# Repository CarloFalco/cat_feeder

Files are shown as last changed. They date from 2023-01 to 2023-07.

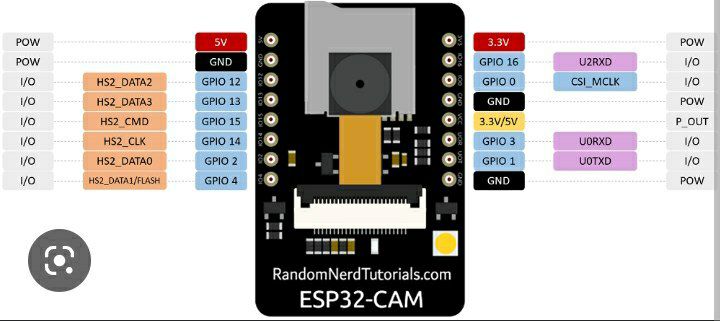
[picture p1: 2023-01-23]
EspCam_pinout.jpg

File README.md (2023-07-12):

# cat food dispenser 
| Cartella 		| Contenuto 		|
| --- 		| --- 			|
| 3D Model  	| File da stampare 	|
| Code  		| Codice 			|

## Requirements list:
- Webcam that allows you to take a photo on demand, and send it on telegram
- Proximity sensor that if it detects something in range takes a photo and sends it on telegram
- Food if requested by telegram dispenses food, every time it is asked it dispenses at least 20 kibbles
- Cap, it won't come off if dropped
- Power supply via usb cable
- System to vicariate it to the ground

## Component list:
1. [AM312](https://it.aliexpress.com/item/32921030810.html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)
1. [DS3230-180](https://it.aliexpress.com/item/1943129663.html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)
1. [ESP32-CAM-MB](https://it.aliexpress.com/item/1005003334474586.html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)
1. [OV2640-160/650nm](https://it.aliexpress.com/item/1005004518669324.html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)

## Printing component:

|  		|  		| 	|	|	||
| ---|--- | ---| ---|--- |--- |
| 1 | Hopper			| 76g 	| |7h 	|
| 2 | PortionWheel 		| 41g	| |4h 	|
| 3 | WheelCompartment 	| 59g	| |5h 	|
| 4 | electronic 		| 151g	| |16h 	|
| 5 | Bowl 				| 146g	| |15h 	|
| 6 | Shel 				| 214g	| |20h 	|
| 7 | Lid 				| 61g	| |5h 	|
| | 				| 		| |		|
|  		|  		|  748g	| |72h	|

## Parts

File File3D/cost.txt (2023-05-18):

1 	hopper 				76g 	7h
2	PortionWheel		41g		4h
3	wheelCompartment	59g		5h
4	electronic			151g	16h
5	Blow 				146g	15h
6	shel				214g	20h
7 	lid					61g		5h

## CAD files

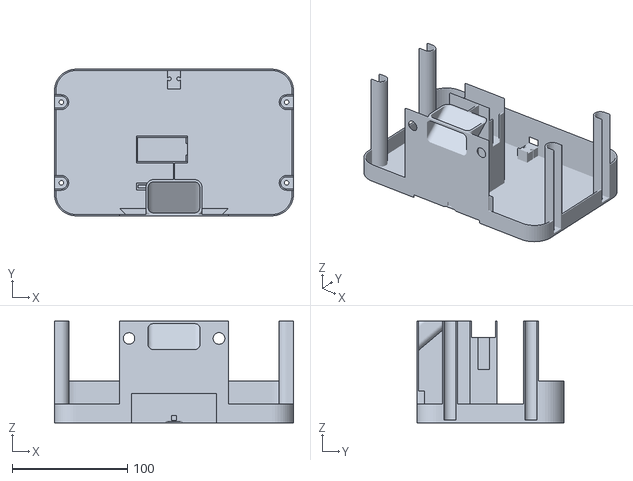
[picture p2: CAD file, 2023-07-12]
File3D/4-ElectronicsCompartment_V3.stl
207.2 x 127.2 x 88.2

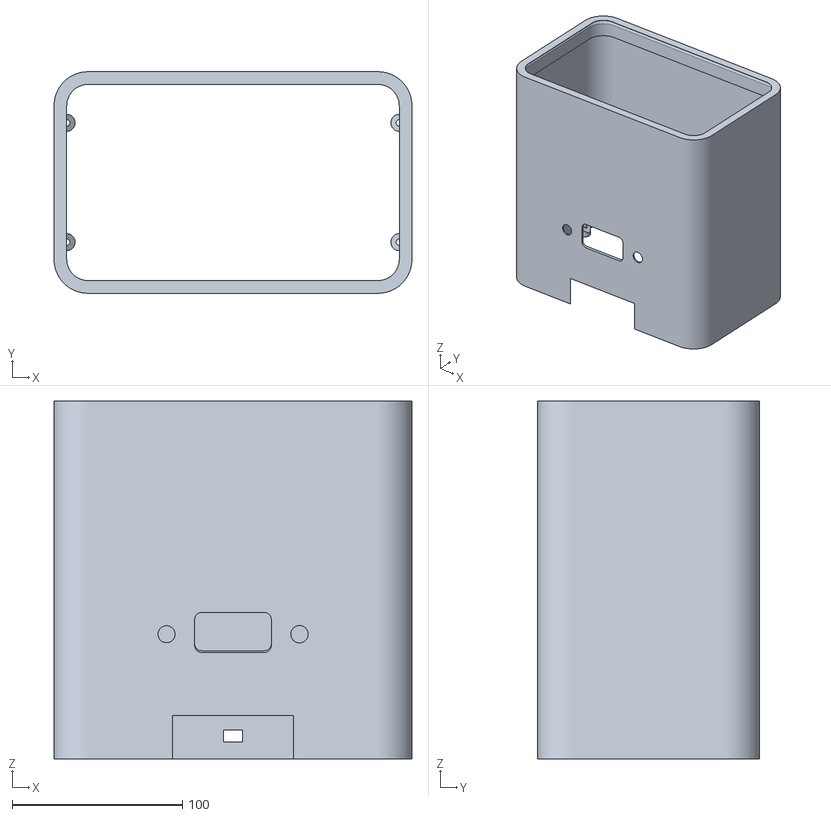
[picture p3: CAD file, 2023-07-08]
File3D/6-Shell_V2.stl
210.0 x 130.0 x 210.0

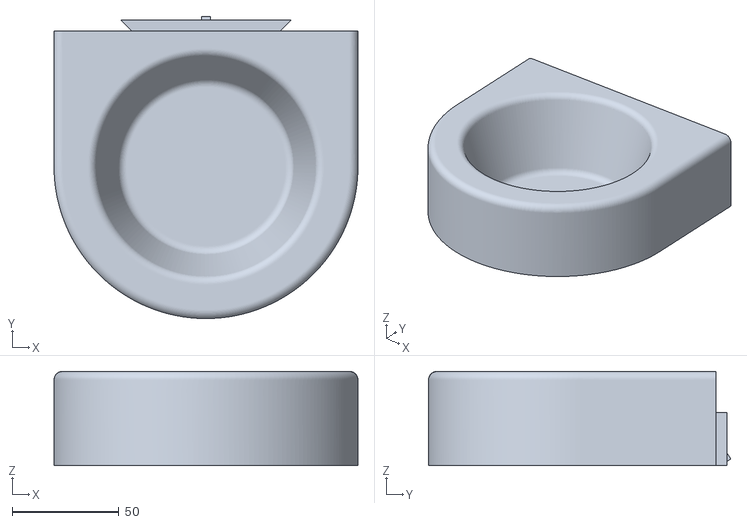
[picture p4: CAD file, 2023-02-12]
File3D/5-Bowl-103mm-diameter.stl
142.5 x 141.6 x 44.2

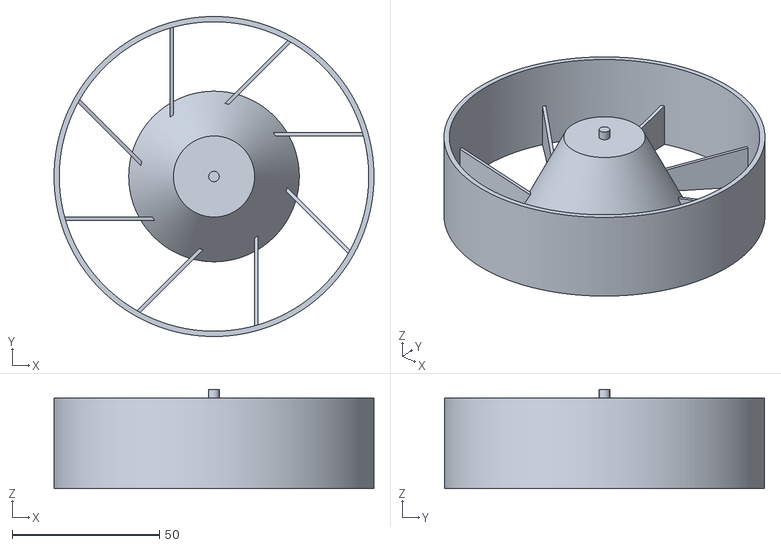
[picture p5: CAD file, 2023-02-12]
File3D/2-PortionWheel.stl
108.8 x 108.8 x 33.8

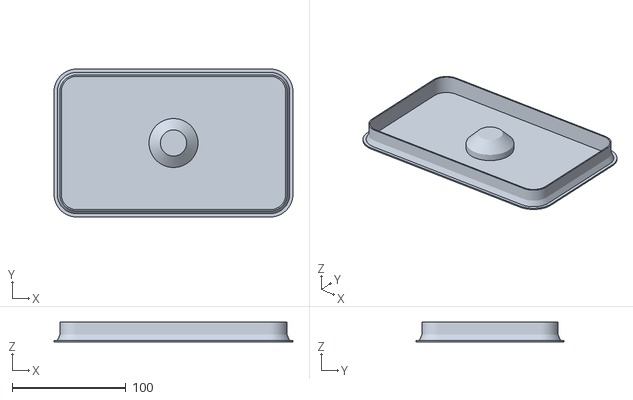
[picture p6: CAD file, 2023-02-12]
File3D/7-Lid.stl
210.0 x 130.0 x 17.2

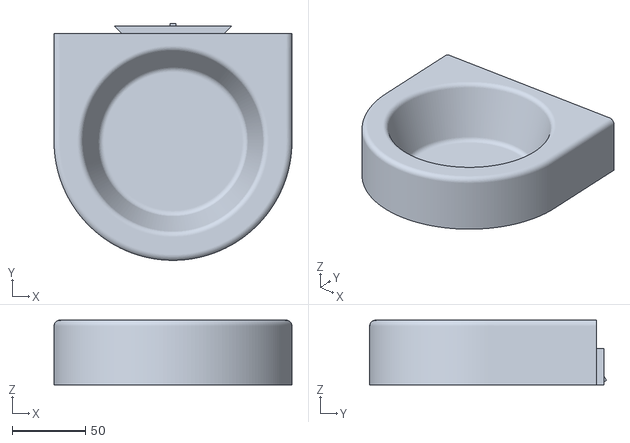
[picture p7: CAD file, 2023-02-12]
File3D/5-Bowl-123mm-diameter.stl
162.5 x 161.6 x 44.2

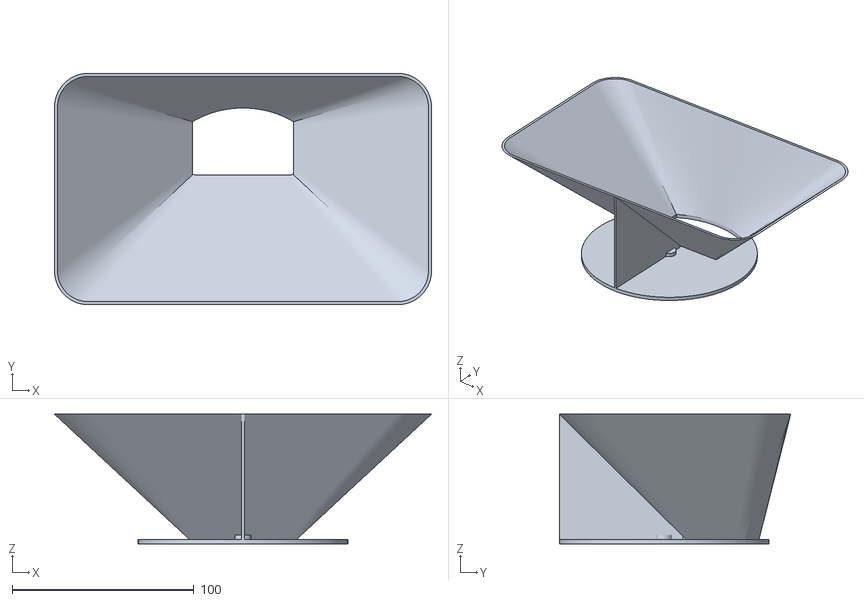
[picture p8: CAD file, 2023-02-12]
File3D/1-Hopper.stl
207.2 x 127.2 x 71.2

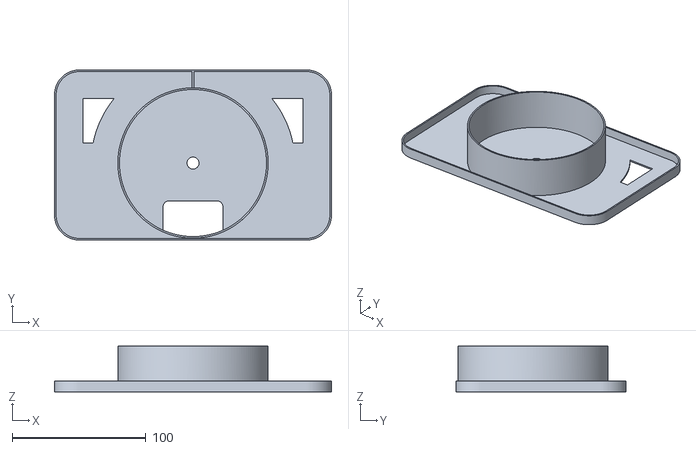
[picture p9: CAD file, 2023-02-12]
File3D/3-WheelCompartment.stl
207.2 x 127.2 x 34.4

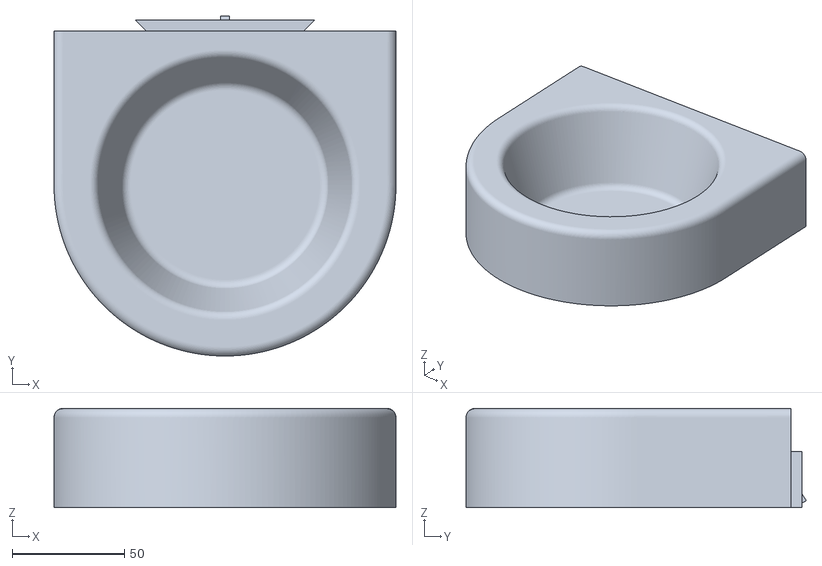
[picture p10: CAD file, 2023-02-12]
File3D/5-Bowl-113mm-diameter-default.stl
152.5 x 151.6 x 44.2

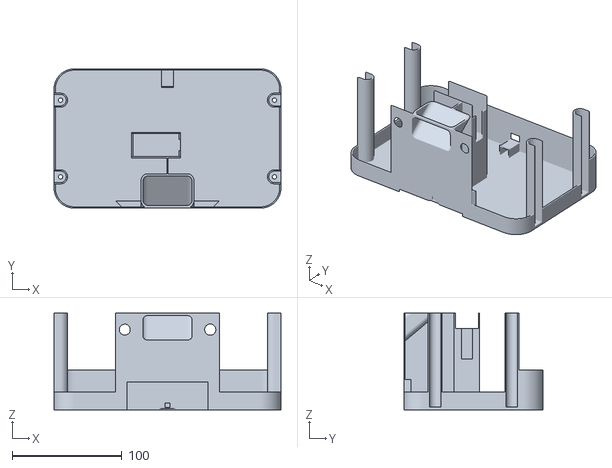
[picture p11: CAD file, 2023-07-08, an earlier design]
File3D/4-ElectronicsCompartment_V2.stl
207.2 x 127.2 x 88.2

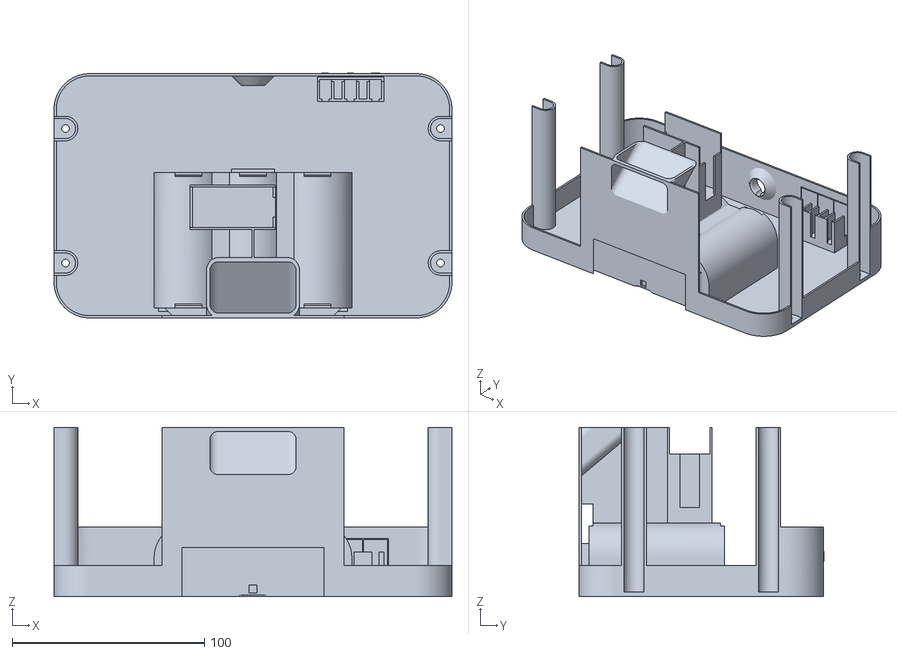
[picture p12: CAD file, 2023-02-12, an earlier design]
File3D/4-ElectronicsCompartment.stl
207.2 x 127.5 x 88.2

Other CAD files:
File3D/6-Shell.stl
File3D/FatPetFeeder-v4.40.f3d
File3D/FeederShell.f3d
File3D/PortaCrocchette.f3d

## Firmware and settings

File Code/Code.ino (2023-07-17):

#include <Arduino.h>
#include <WiFi.h>
#include <WiFiClientSecure.h>
#include "soc/soc.h"
#include "soc/rtc_cntl_reg.h"
#include "esp_camera.h"
#include <UniversalTelegramBot.h>
#include <ArduinoJson.h>

#include <freertos/FreeRTOS.h>
#include <freertos/task.h>
#include <ESP32Servo.h>

#include <EEPROM.h>
// Use @myidbot to find out the chat ID of an individual or a group
// Also note that you need to click "start" on a bot before it can
// message you

#include "Credential.h"

// FLASH
#define FLASH_LED_PIN 4
// SERVOMOTORE
#define MOS_SERVO_PIN 2
#define FEED_MAX_COUNT 6
#define SERVO_PIN 13
#define SERVO_MOVE_ON 95
#define SERVO_MOVE_OFF 90
#define FEED_INIT_COUNT 2
// SENSORE IR
#define IR_PIN 14
#define IR_DELAY 60  // tempo di delay tra un rilevamento ed un altro


// DEFINE FOR DEBUG
#define DEBUG_WIFI
#define DEBUG_FEEDER
#define DEBUG_NOTIFICATION


TaskHandle_t task1Handle;
TaskHandle_t task2Handle;
TaskHandle_t task3Handle;

typedef struct {
  String CurrentPhotoReqId;  // ID del utente che ha richiesto la foto
  String AuthId[4];          // ID degli utenti
  bool NotificationId[4];    // Flag di abilitazione notifiche utenti [1/0] abilitato/non abilitato

  bool stateIRpin;      // stato del sensore infrarossi
  bool stateSendPhoto;  // stato richiesta di foto
  bool stateFeedCat;    // stato richiesta feedcat
  bool stateFlash;      // stato flash
  int feedCount;        // quantità di cibo
  int eprom_good;       // eeprom non corrotta

} MyStruct;

MyStruct myStruct;

WiFiClientSecure clientTCP;

String BOTtoken = String(BOTtokenKey);
UniversalTelegramBot bot(BOTtoken, clientTCP);

Servo myservo;  // create servo object to control a servo

//Checks for new messages every 1 second.
int botRequestDelay = 500;
unsigned long lastTimeBotRan;

//Checks for new messages every 60 second.
int NotRequestDelay = IR_DELAY * 1000;
unsigned long lastTimeNot;

bool savetoEEPROM = false;

//CAMERA_MODEL_AI_THINKER
#define PWDN_GPIO_NUM 32
#define RESET_GPIO_NUM -1
#define XCLK_GPIO_NUM 0
#define SIOD_GPIO_NUM 26
#define SIOC_GPIO_NUM 27

#define Y9_GPIO_NUM 35
#define Y8_GPIO_NUM 34
#define Y7_GPIO_NUM 39
#define Y6_GPIO_NUM 36
#define Y5_GPIO_NUM 21
#define Y4_GPIO_NUM 19
#define Y3_GPIO_NUM 18
#define Y2_GPIO_NUM 5
#define VSYNC_GPIO_NUM 25
#define HREF_GPIO_NUM 23
#define PCLK_GPIO_NUM 22

void initWiFi_PwrOn(const char* ssid, const char* password) {
  WiFi.mode(WIFI_STA);
  WiFi.begin(ssid, password);
  clientTCP.setCACert(TELEGRAM_CERTIFICATE_ROOT);  // Add root certificate for api.telegram.org

  // Attesa della connessione
  while (WiFi.status() != WL_CONNECTED) {
    delay(1000);
#ifdef DEBUG_WIFI
    Serial.println("Connessione in corso...");
#endif
  }

#ifdef DEBUG_WIFI
  Serial.println("WiFi connected to " + String(ssid));
  Serial.println(WiFi.localIP());
#endif
}

// FUNZIONI RELATIVE ALLA EEPROM
void do_eprom_read() {

  EEPROM.begin(200);
  EEPROM.get(0, myStruct);

  if (myStruct.eprom_good == 11) {
    Serial.println("Good settings in the EPROM ");

    Serial.print("Notification: ");
    for (int i = 0; i < 4; i++) {
      Serial.print("\t");
      Serial.print(myStruct.NotificationId[i]);
    }
    Serial.println(".");

    Serial.println(myStruct.CurrentPhotoReqId);
    Serial.print("State IR: ");
    Serial.println(myStruct.stateIRpin);
    Serial.print("State sendphoto: ");
    Serial.println(myStruct.stateSendPhoto);
    Serial.print("State feedcat: ");    
    Serial.println(myStruct.stateFeedCat);
    Serial.print("State Flash: ");   
    Serial.println(myStruct.stateFlash);
    Serial.print("Count Num: ");
    Serial.println(myStruct.feedCount);

  } else {
    Serial.println("EPROM canot be read ");
    myStruct = {
      String(""),
      { String(CHAT_ID_1), String(CHAT_ID_2), String(""), String("") },
      { 1, 0, 0, 0 },
      false,                //stateIRpin
      false,                //stateSendPhoto
      false,                //stateFeedCat
      LOW,                  // stato flash
      FEED_INIT_COUNT,      // tempo di feed
      11                    // stato EEPROM
    };
    do_eprom_write();
  }
}

void do_eprom_write() {
  Serial.println("Writing to EPROM ...");
  EEPROM.begin(200);
  EEPROM.put(0, myStruct);
  EEPROM.commit();
  EEPROM.end();
}

// FUNZIONI RELATIVE ALLA FOTOCAMERA
void configInitCamera() {
  camera_config_t config;
  config.ledc_channel = LEDC_CHANNEL_0;
  config.ledc_timer = LEDC_TIMER_0;
  config.pin_d0 = Y2_GPIO_NUM;
  config.pin_d1 = Y3_GPIO_NUM;
  config.pin_d2 = Y4_GPIO_NUM;
  config.pin_d3 = Y5_GPIO_NUM;
  config.pin_d4 = Y6_GPIO_NUM;
  config.pin_d5 = Y7_GPIO_NUM;
  config.pin_d6 = Y8_GPIO_NUM;
  config.pin_d7 = Y9_GPIO_NUM;
  config.pin_xclk = XCLK_GPIO_NUM;
  config.pin_pclk = PCLK_GPIO_NUM;
  config.pin_vsync = VSYNC_GPIO_NUM;
  config.pin_href = HREF_GPIO_NUM;
  config.pin_sccb_sda = SIOD_GPIO_NUM;
  config.pin_sccb_scl = SIOC_GPIO_NUM;
  config.pin_pwdn = PWDN_GPIO_NUM;
  config.pin_reset = RESET_GPIO_NUM;
  config.xclk_freq_hz = 24000000;
  config.pixel_format = PIXFORMAT_JPEG;  //YUV422,GRAYSCALE,RGB565,JPEG
  config.grab_mode = CAMERA_GRAB_LATEST;
  config.frame_size = FRAMESIZE_HD;  // FRAMESIZE_ + QVGA|CIF|VGA|SVGA|XGA|SXGA|UXGA
  config.jpeg_quality = 10;          //10-63 lower number means higher quality
  config.fb_count = 4;

  // camera init
  esp_err_t err = esp_camera_init(&config);
  if (err != ESP_OK) {
    Serial.printf("Camera init failed with error 0x%x", err);
    delay(1000);
    ESP.restart();
  }

  // Drop down frame size for higher initial frame rate
  sensor_t* s = esp_camera_sensor_get();
  s->set_framesize(s, FRAMESIZE_HD);        // UXGA|SXGA|XGA|SVGA|VGA|CIF|QVGA|HQVGA|QQVGA
  s->set_brightness(s, 0);                  // -2 to 2
  s->set_contrast(s, 0);                    // -2 to 2
  s->set_saturation(s, 0);                  // -2 to 2
  s->set_special_effect(s, 0);              // 0 to 6 (0 - No Effect, 1 - Negative, 2 - Grayscale, 3 - Red Tint, 4 - Green Tint, 5 - Blue Tint, 6 - Sepia)
  s->set_whitebal(s, 1);                    // 0 = disable , 1 = enable
  s->set_awb_gain(s, 1);                    // 0 = disable , 1 = enable
  s->set_wb_mode(s, 0);                     // 0 to 4 - if awb_gain enabled (0 - Auto, 1 - Sunny, 2 - Cloudy, 3 - Office, 4 - Home)
  s->set_exposure_ctrl(s, 1);               // 0 = disable , 1 = enable
  s->set_aec2(s, 0);                        // 0 = disable , 1 = enable
  s->set_ae_level(s, 0);                    // -2 to 2
  s->set_aec_value(s, 300);                 // 0 to 1200
  s->set_gain_ctrl(s, 1);                   // 0 = disable , 1 = enable
  s->set_agc_gain(s, 0);                    // 0 to 30
  s->set_gainceiling(s, (gainceiling_t)0);  // 0 to 6
  s->set_bpc(s, 0);                         // 0 = disable , 1 = enable
  s->set_wpc(s, 1);                         // 0 = disable , 1 = enable
  s->set_raw_gma(s, 1);                     // 0 = disable , 1 = enable
  s->set_lenc(s, 1);                        // 0 = disable , 1 = enable
  s->set_hmirror(s, 0);                     // 0 = disable , 1 = enable
  s->set_vflip(s, 0);                       // 0 = disable , 1 = enable
  s->set_dcw(s, 1);                         // 0 = disable , 1 = enable
  s->set_colorbar(s, 0);                    // 0 = disable , 1 = enable
  s->set_colorbar(s, 0);                    // 0 = disable , 1 = enable
}

String sendPhotoTelegram() {
  const char* myDomain = "api.telegram.org";
  String getAll = "";
  String getBody = "";

  camera_fb_t* fb = NULL;
  fb = esp_camera_fb_get();
  if (!fb) {
    Serial.println("Camera capture failed");
    delay(1000);
    ESP.restart();
    return "Camera capture failed";
  }

  Serial.println("Connect to " + String(myDomain));


  if (clientTCP.connect(myDomain, 443)) {
    Serial.println("Connection successful");
    Serial.println("Sending Photo to: " + myStruct.CurrentPhotoReqId);

    String head = "--EOF\r\nContent-Disposition: form-data; name=\"chat_id\"; \r\n\r\n" + myStruct.CurrentPhotoReqId + "\r\n--EOF\r\nContent-Disposition: form-data; name=\"photo\"; filename=\"esp32-cam.jpg\"\r\nContent-Type: image/jpeg\r\n\r\n";
    String tail = "\r\n--EOF--\r\n";

    uint16_t imageLen = fb->len;
    uint16_t extraLen = head.length() + tail.length();
    uint16_t totalLen = imageLen + extraLen;

    clientTCP.println("POST /bot" + BOTtoken + "/sendPhoto HTTP/1.1");
    clientTCP.println("Host: " + String(myDomain));
    clientTCP.println("Content-Length: " + String(totalLen));
    clientTCP.println("Content-Type: multipart/form-data; boundary=EOF");
    clientTCP.println();
    clientTCP.print(head);

    uint8_t* fbBuf = fb->buf;
    size_t fbLen = fb->len;
    for (size_t n = 0; n < fbLen; n = n + 1024) {
      if (n + 1024 < fbLen) {
        clientTCP.write(fbBuf, 1024);
        fbBuf += 1024;
      } else if (fbLen % 1024 > 0) {
        size_t remainder = fbLen % 1024;
        clientTCP.write(fbBuf, remainder);
      }
    }

    clientTCP.print(tail);

    esp_camera_fb_return(fb);

    int waitTime = 10000;  // timeout 10 seconds
    long startTimer = millis();
    boolean state = false;

    while ((startTimer + waitTime) > millis()) {
      Serial.print(".");
      delay(100);
      while (clientTCP.available()) {
        char c = clientTCP.read();
        if (state == true) getBody += String(c);
        if (c == '\n') {
          if (getAll.length() == 0) state = true;
          getAll = "";
        } else if (c != '\r')
          getAll += String(c);
        startTimer = millis();
      }
      if (getBody.length() > 0) break;
    }
    clientTCP.stop();
    Serial.println(getBody);
  } else {
    getBody = "Connected to api.telegram.org failed.";
    Serial.println("Connected to api.telegram.org failed.");
  }
  return getBody;
}

String sendPhotoTelegramAll() {
  int SenderNum = sizeof(myStruct.NotificationId) / sizeof(bool);

  int maxNum = 0;

  for (int i = 0; i < SenderNum; i++) {
    if (myStruct.NotificationId[i]) {
      maxNum = 1;
      break;
    }
  }

  if (!maxNum) {
    Serial.println("No candidate for photo");
    return "No candidate for photo";
  }

  const char* myDomain = "api.telegram.org";
  String getAll = "";
  String getBody = "";

  camera_fb_t* fb = NULL;
  fb = esp_camera_fb_get();
  if (!fb) {
    Serial.println("Camera capture failed");
    delay(1000);
    ESP.restart();
    return "Camera capture failed";
  }

  Serial.println("Connect to " + String(myDomain));
  for (int i = 0; i < SenderNum; i++) {

    // printf("%d\n", myStruct.Notification[i]);
    if (myStruct.NotificationId[i]) {
      Serial.println("Sending Photo to: " + myStruct.AuthId[i]);
      // Sending notification to Id
      String chat_id = myStruct.AuthId[i];
      bot.sendMessage(chat_id, "Motion Detected", "Markdown");


      if (clientTCP.connect(myDomain, 443)) {  // FUNZIONE CHE INVIA LA FOTO AL ID i-esimo
        Serial.println("Connection successful");

        String head = "--EOF\r\nContent-Disposition: form-data; name=\"chat_id\"; \r\n\r\n" + myStruct.AuthId[i] + "\r\n--EOF\r\nContent-Disposition: form-data; name=\"photo\"; filename=\"esp32-cam.jpg\"\r\nContent-Type: image/jpeg\r\n\r\n";
        String tail = "\r\n--EOF--\r\n";

        uint16_t imageLen = fb->len;
        uint16_t extraLen = head.length() + tail.length();
        uint16_t totalLen = imageLen + extraLen;

        clientTCP.println("POST /bot" + BOTtoken + "/sendPhoto HTTP/1.1");
        clientTCP.println("Host: " + String(myDomain));
        clientTCP.println("Content-Length: " + String(totalLen));
        clientTCP.println("Content-Type: multipart/form-data; boundary=EOF");
        clientTCP.println();
        clientTCP.print(head);

        uint8_t* fbBuf = fb->buf;
        size_t fbLen = fb->len;
        for (size_t n = 0; n < fbLen; n = n + 1024) {
          if (n + 1024 < fbLen) {
            clientTCP.write(fbBuf, 1024);
            fbBuf += 1024;
          } else if (fbLen % 1024 > 0) {
            size_t remainder = fbLen % 1024;
            clientTCP.write(fbBuf, remainder);
          }
        }

        clientTCP.print(tail);



        int waitTime = 10000;  // timeout 10 seconds
        long startTimer = millis();
        boolean state = false;

        while ((startTimer + waitTime) > millis()) {
          Serial.print(".");
          delay(100);
          while (clientTCP.available()) {
            char c = clientTCP.read();
            if (state == true) getBody += String(c);
            if (c == '\n') {
              if (getAll.length() == 0) state = true;
              getAll = "";
            } else if (c != '\r')
              getAll += String(c);
            startTimer = millis();
          }
          if (getBody.length() > 0) break;
        }
        clientTCP.stop();
        Serial.println(getBody);
      } else {
        getBody = "Connected to api.telegram.org failed.";
        Serial.println("Connected to api.telegram.org failed.");
      }
    }
  }
  esp_camera_fb_return(fb);

  return getBody;
}

// FUNZIONI RELATIVE AL SERVO MOTORE
void ServoFeed_PwrOn(void) {
  ESP32PWM::allocateTimer(0);
  ESP32PWM::allocateTimer(1);
  ESP32PWM::allocateTimer(2);
  ESP32PWM::allocateTimer(3);
  myservo.setPeriodHertz(50);             // standard 50 hz servo
  myservo.attach(SERVO_PIN, 1000, 2000);  // attaches the servo on pin 18 to the servo object

  myservo.write(SERVO_MOVE_OFF);

  pinMode(MOS_SERVO_PIN, OUTPUT);
  digitalWrite(MOS_SERVO_PIN, LOW);
}

void ServoFeed_tsk1S(void) {
  static int CountFeed;
  #ifdef DEBUG_FEEDER
  Serial.print(CountFeed);
  Serial.println("<- Valore in ingresso;");
  #endif

  if (myStruct.stateFeedCat == 1) {
    if (CountFeed == 1) {
      digitalWrite(MOS_SERVO_PIN, HIGH);
    }
    myservo.write(SERVO_MOVE_ON);
    CountFeed = CountFeed + 1;
#ifdef DEBUG_FEEDER
    Serial.print("Debug State = ");
    Serial.println("1");
#endif
  }

  if (CountFeed > myStruct.feedCount) {
    myservo.write(SERVO_MOVE_OFF);

    digitalWrite(MOS_SERVO_PIN, LOW);
    myStruct.stateFeedCat = 0;
    CountFeed = 0;
#ifdef DEBUG_FEEDER
    Serial.print("Debug State = ");
    Serial.println("2");
#endif
  }
}

// FUNZIONI RELATIVE AL SENSORE IR
void IR_PwrOn(void) {
  // definizione tipologia pin
  pinMode(IR_PIN, INPUT_PULLUP);
  // condizione iniziale IR
  myStruct.stateIRpin = digitalRead(IR_PIN);
}

int IR_Tsk(void) {
  static unsigned long lastDebounceTime;
  static int pinState_kp;
  static int pinState;
  // Leggi lo stato del pin
  int reading = digitalRead(IR_PIN);

  // Verifica se il pin è diverso dall'ultimo stato registrato
  if (reading != pinState_kp) {
    // Aggiorna il tempo di debounce
    lastDebounceTime = millis();
  }

  // Verifica se è trascorso il tempo di debounce
  if ((millis() - lastDebounceTime) > 50) {
    // Se il valore del pin è stabile, aggiorna lo stato corrente
    if (reading != pinState) {
      pinState = reading;

      // Se lo stato del pulsante è 1 (passaggio da 0 a 1), stampa sul monitor seriale
      if (pinState == HIGH) {
        Serial.println("Il pulsante è stato premuto");
        // TODO: QUI ANDREBBE MESSO IL CECK SULLE NOTIFICHE
        int SenderNum = sizeof(myStruct.NotificationId) / sizeof(bool);
        int maxNum = 0;
        for (int i = 0; i < SenderNum; i++) {
          if (myStruct.NotificationId[i]) {
            maxNum = 1;
            break;
          }
        }
        if (maxNum) {
          myStruct.stateIRpin = true;
        }
      }
    }
  }
  // Salva lo stato attuale del pulsante per il prossimo ciclo
  pinState_kp = reading;
  return pinState;
}

// FUNZIONI RELATIVE AL BOT
void handleNewMessages(int numNewMessages) {
  Serial.print("Handle New Messages: ");
  Serial.println(numNewMessages);

  for (int i = 0; i < numNewMessages; i++) {
    String chat_id = String(bot.messages[i].chat_id);


    // verifico che sia un utente autorizzato
    int checkIdAuth = 0;
    int j = 0;
    for (j = 0; j < sizeof(myStruct.AuthId); j++) {  // TODO
      if (chat_id == myStruct.AuthId[j]) {
        checkIdAuth = 1;
        break;
      }
    }
    if (!checkIdAuth) {
      bot.sendMessage(chat_id, "Unauthorized user", "");
      continue;
    }

    // Print the received message
    String text = bot.messages[i].text;
    Serial.println(text);

    String from_name = bot.messages[i].from_name;

    if (text == "/feed") {
      myStruct.stateFeedCat = true;
      bot.sendMessage(chat_id, "I will feed the cat.\n", "Markdown");
    }
    if (text == "/flash") {
      myStruct.stateFlash = !myStruct.stateFlash;
      digitalWrite(FLASH_LED_PIN, myStruct.stateFlash);
      Serial.println("Change flash LED state");
    }
    if (text == "/photo") {
      myStruct.stateSendPhoto = true;
      myStruct.CurrentPhotoReqId = chat_id;
      Serial.println("New photo request");
    }
    if (text == "/start" || text == "/back") {
      String welcome = "Welcome to the ESP32-CAM Telegram bot.\n";
      welcome += "/photo : takes a new photo\n";
      welcome += "/flash : toggle flash LED\n";
      welcome += "/feed : feed the cat\n";
      welcome += "/settings : possibily to modify basic setting\n";
      welcome += "You'll receive a photo whenever motion is detected.\n";
      bot.sendMessage(chat_id, welcome, "Markdown");
    }
    if (text == "/settings") {  // TODO: IMPLEMENTARE LE FUNZIONALITA
      String welcome = "In this menu, you can change information about the dispenser.\n";
      welcome = "/notification, here you can change notification settings.\n";
      welcome += "/setfeed : Change food quantity\n";
      welcome += "/back : back to start menu\n";
      bot.sendMessage(chat_id, welcome, "Markdown");
    }
    if (text == "/setfeed") {  // Funzionalità legate alle feeder
      String welcome = "/setfeed, here you can increase or decrease food quantity.\n";
      welcome += "/increase : Increase food quantity\n";
      welcome += "/decrease : Decrease food quantity\n";
      welcome += "/back : back to start menu\n";
      bot.sendMessage(chat_id, welcome, "Markdown");
    }
    if (text == "/increase") {
      if (myStruct.feedCount < FEED_MAX_COUNT) {
        // vado a modificare il valore
        myStruct.feedCount++;

        Serial.print("feedCount: ");
        Serial.println(myStruct.feedCount);
        // vado a salvare il valore in eeprom
        savetoEEPROM = true;
      } else {
        Serial.println("you reach the maximum value");
      }
    }
    if (text == "/decrease") {
      if (myStruct.feedCount > 1) {
        // vado a modificare il valore
        myStruct.feedCount--;
        Serial.print("feedCount: ");
        Serial.println(myStruct.feedCount);
        // vado a salvare il valore in eeprom
        savetoEEPROM = true;
      } else {
        Serial.println("you reach the minimum value");
      }
    }
    if (text == "/notification") {  // Funzionalità legate alle notifiche
      String welcome = "/notification, here you can change notification settings.\n";
      welcome += "/dontshutup : enable motion sensor notification\n";
      welcome += "/shutup : disalbe motion sensor notification\n";
      welcome += "/back : back to start menu\n";
      bot.sendMessage(chat_id, welcome, "Markdown");
    }
    if (text == "/shutup") {
      // controllo se il valore precedente è differente da quello che ho chiesto
      if (myStruct.NotificationId[j] == true) {
        // vado a modificare il valore
        myStruct.NotificationId[j] = false;
        // vado a salvare il valore in eeprom
        savetoEEPROM = true;
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
void loop() {

  if (millis() > lastTimeNot + NotRequestDelay & myStruct.stateIRpin) {
    int numNewMessages = bot.getUpdates(bot.last_message_received + 1);
    // TODO: va pensato ad un modo per non chiamare due funzioni contemporaneamente
    Serial.println("Preparing photo");
    sendPhotoTelegramAll();
    myStruct.stateIRpin = false;
    lastTimeNot = millis();
  }


  if (myStruct.stateSendPhoto) {
    Serial.println("Preparing photo");
    sendPhotoTelegram();
    myStruct.stateSendPhoto = false;
    myStruct.CurrentPhotoReqId = "";
  }

  if (millis() > lastTimeBotRan + botRequestDelay) {
    int numNewMessages = bot.getUpdates(bot.last_message_received + 1);
    while (numNewMessages) {
      Serial.println("got response");
      handleNewMessages(numNewMessages);
      numNewMessages = bot.getUpdates(bot.last_message_received + 1);
    }
    lastTimeBotRan = millis();
  }
}



// CONDIZIONI INIZIALI//
void Scheduler_PwrOn(void) {
  xTaskCreatePinnedToCore(
    task1,         // Task function.
    "Task1",       // name of task.
    2048,          // Stack size of task
    NULL,          // parameter of the task
    1,             // priority of the task
    &task1Handle,  // Task handle to keep track of created task
    1);            // pin task to core 0

  xTaskCreatePinnedToCore(
    task2,         // Task function.
    "Task2",       // name of task.
    2048,          // Stack size of task
    NULL,          // parameter of the task
    1,             // priority of the task
    &task2Handle,  // Task handle to keep track of created task
    1);            // pin task to core 1

  xTaskCreatePinnedToCore(
    task3,         // Task function.
    "Task3",       // name of task.
    2048,          // Stack size of task
    NULL,          // parameter of the task
    1,             // priority of the task
    &task3Handle,  // Task handle to keep track of created task
    1);            // pin task to core 1
  /*                    
  xTaskCreatePinnedToCore(
                     KeepWiFiAlive,
                    "Keep WiFi Alive",     // name of task. 
                    2048,       // Stack size of task 
                    NULL,        // parameter of the task 
                    1,           // priority of the task 
                    &task4Handle,      // Task handle to keep track of created task 
                    1);          // pin task to core 1 
  */
}

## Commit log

2022-12-17 Start working on Add stl File3D
    [Blades.stl, Cap.stl, Case_top.stl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]
2022-12-28 Testato - Connessione Wifi - Connessione Telegram
    [Body1.stl, Coperchio.stl, PortaCrocchette.stl]
2022-12-28 Aggiunto e testato il sistema di Feed
2023-01-15 nuovo micro, inizio la parte delle foto
    [Body1.stl]
2023-01-16 - Caricato il sw per scattare le foto e le invia su telegram, - fatto il merge con wifi manager - testato il bot, e il sensore di movimento
    TODO:
    - le foto non vengono inviate su Telegram
    - va integrato il servomotore (molto probabile un conflitto in un typedef)
2023-01-23 In questa versione: - Abbandonato l'utilizzo di platformio - Finito la parte di wifi/ telegram con la nuova funzione di PwrOn - Preparato il setup del bot telegrm - Creato la funzione legata alla vid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
    TO DO:
    - aggiungere le funzioni per il servomootre
    - verificare la funzione che disabilita il sensore di movimento
    [Code.ino]
2023-02-07 Aggiunto il feeder, e sistemati i task
2023-02-11 aggiunto il secondo ID telegram Fix bug minori
    [Code.ino]
2023-02-12 piccole modifiche, ma ancora crasha
    [Code.ino]
2023-02-12 Cambiato file 3d, fatti alcuni test sul servo motore
    [1-Hopper.stl, 2-PortionWheel.stl, 3-WheelCompartment.stl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]
2023-05-18 Versione funzionante, c'e ancora qualche problema con il sensore di prossimita, e la risoluzione della videocamera
    [8-BatteryCover.stl]
2023-05-25 testato con nuovo servomotore. - /photo -> Tested - /feed -> Tested - /flash -> Tested - /shutdup -> Working - /dontshutup -> Working
    ho aggiunto il programma per testare il sensore infrarossi
2023-06-22 primo test con platformio e ESP 32, blink led
2023-06-22 secondo commit, con scheda Esp32CAM
2023-06-22 Integrata la libreria myFcn.h, e provato il monitor seriale
2023-06-23 Aggiunto Wifi, e task per tenere sempre on il wifi. Nuova funzione per il debug del servo motore
2023-06-23 Commit after merge
    [1-Hopper.stl, 2-PortionWheel.stl, 3-WheelCompartment.stl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]
2023-07-03 Pre branck, funzionante (Servo, sensore IR, internet, Taks) Non Funzionante(Telegram)
2023-07-08 I start over, using only arduino ide. 3D files are loaded
    [1-Hopper.stl, 2-PortionWheel.stl, 3-WheelCompartment.stl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]
2023-07-08 Update V 1.2: Infrared sensor added, Changes to eeprom operation, to lighten the message handler New messages added
2023-07-08 Update V 1.2: Added sending of photos if motion is detected Added the possibility to change the amount of kibble from telegram Set the time between IR sensor notifications
2023-07-12 Aggiunto mosfet per spegnere il servomotore, modificato il modello della base
    [4-ElectronicsCompartment_V3.stl, FeederShell.f3d, PortaCrocchette.f3d]
